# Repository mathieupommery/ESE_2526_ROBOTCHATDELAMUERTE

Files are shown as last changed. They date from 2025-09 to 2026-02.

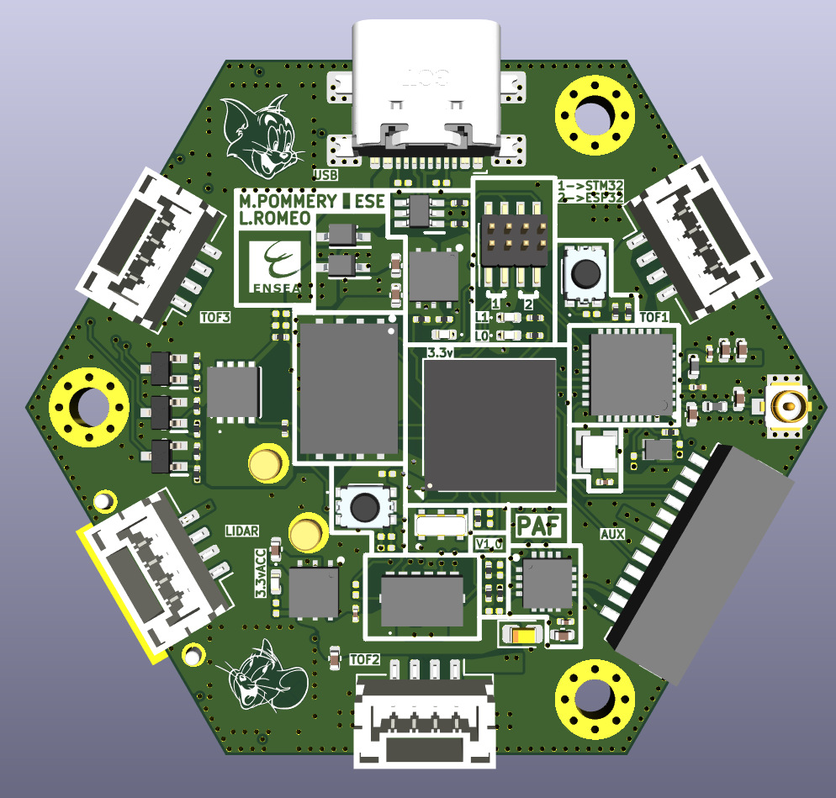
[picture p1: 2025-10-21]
DOCS/IMG README/MB_v1_front.png

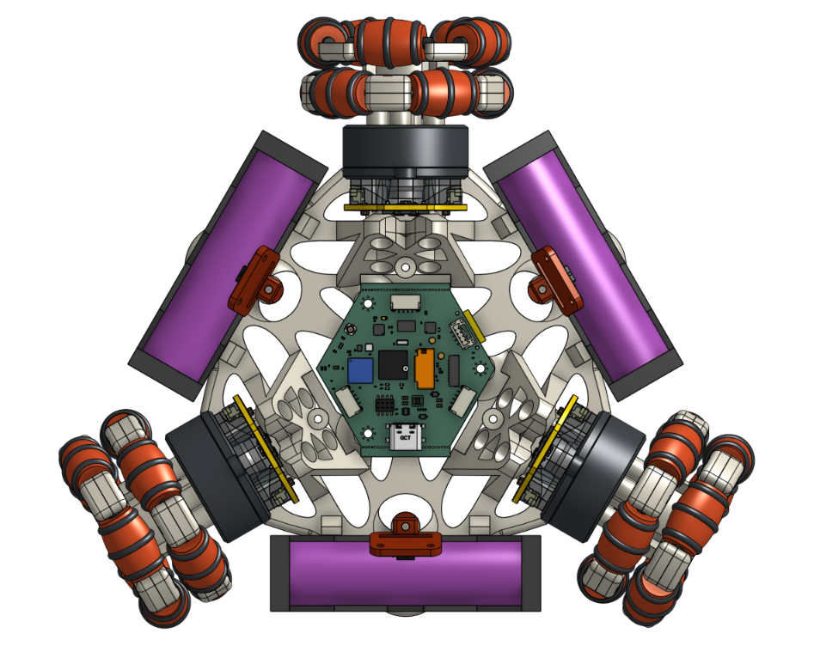
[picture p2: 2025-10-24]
DOCS/IMG README/Robot top PCB view.png

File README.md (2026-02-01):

# Cat-and-Mouse Robot Project

## Table of contents
1. [Introduction](#1-introduction)
2. [FOC omniwheel](#2-foc-omniwheel)
   1. [Hardware](#21-hardware)
      1. [Electronics](#211-electronics)
      2. [Mechanics](#212-mechanics)
   2. [Software (Overview)](#22-software-overview)
   3. [Bottleneck](#23-bottleneck)
3. [DC omniwheel](#3-dc-omniwheel)
   1. [New Motor control PCB](#31-new-motor-control-pcb)
   2. [Adapting the frame to allocate new DC motors, and more...](#32-adapting-the-frame-to-allocate-new-dc-motors-and-more)
   3. [Movement strategy](#33-movement-strategy)
      1. [Cat mode](#331-cat-mode)
      2. [Mouse mode](#332-mouse-mode)
   4. [Issues](#34-issues)
4. [Regular DC](#4-regular-dc)
   1. [Hardware](#41-hardware)
5. [Strategy Implementation](#5-strategy-implementation)
   1. [Overview of Cat/Mouse Mode](#51-overview-of-cat/mouse-mode)
   2. [LiDAR handling](#52-lidar-handling)
   3. [Motor control](#53-motor-control)
   4. [Additional PIMP mode](#54-additional-pimp-mode)

## 1. Introduction
This project aims to design and build a **mobile robotic system** capable of playing a "cat and mouse" pursuit game.  
It combines **real-time embedded control**, **sensor fusion**, and **mechanical design** to create an autonomous robot capable of chasing or evading another robot in a dynamic environment. 
In addition to that we built ESP32-S3 based audio system with the intent of **listening with a mic** and answering using **AI based model through wifi connection and online server.**

## 2. FOC omniwheel

We first wanted to make a three omniwheeled robot with FOC control on brushless motors.

### 2.1. Hardware

The hardware design is divided into two main parts:

#### 2.1.1. Electronics
The electronic subsystem provides sensing, control, and communication between the robot's components. 

##### Motherboard

###### V1
MB_v1_front

MB_v1_back

**Main features:**
- **Microcontroller:** 480Mhz STM32H743 in TFBGA100 package, 1MB RAM 2MB Flash 
- **Sensors:** ADXL343 accelerometer and 3x TOF sensor 
- **Actuators:** UART COM for each STM32 FOC controller
- **Power Management:** 2.5A 5V buck, separate 3.3V ldo between mcu and accelerometer.  
- **Communication:** SPI / UART / Wireless link via esp32-C6
- **Features:** Up to 1Gb nand flash of 512Mb Nor flash 

This board work perfectly fine on it's own, we upgraded it just for adding option and better looking connector 

###### V2
MB_v2_Front

mb_v2_back

This version improved the audio part by adding a micro sd card wich replaced the previous NOR flash in order to get faster read and write speed and easier data management (indeed nor flash work on 4096 byte secotr that has to be erased before program, it is harder to implement in order to deal with the usb msc protocol and slower) on top of that we moved all the **audio processing into a faster esp32-S3** wich communicates with the stm32 by a uart link, it allows us to get **real AI functionnality** by using wifi link and also communicate with the **STM32 that controls all of the Robot's movements**.  
Finally this board is designed as a two board stack with the FOC controller v2.

**Main features:**
- **Microcontroller:** 480Mhz STM32H743 in TFBGA100 package, 1MB RAM 2MB Flash 
- **Sensors:** ADXL343 accelerometer and 3x TOF sensor, ICS43434 I2S mems microphone 
- **Actuators:** UART COM for each STM32 FOC controller
- **Power Management:** 
-2.5A 5V buck with up to 30v input capability, -separate 3.3V ldo between for accelerometer
-latest 3.3v SIP buck from texas instrument for both mcu
- decoupling caps near motor connector.

- **Communication:** SPI / UART / Wireless link via esp32-s3 (bluetooth 5.0, wifi 2.4G)
- **Features:** Sd card port and esp32-s3 to manage all the audio part with class d amplifier max99357 and microphone in order to get AI to answer via a wifi call to an api. 

##### FOC STM32 based Controller

###### V1

Front_foc_v1
Back_foc_v1


The FOC controller is build arround a Iflight GBM2804H-100T motor, that we will use in direct drive to drive our robot using a 3 Wheel Omniwheel base. 

**Main features:**
- **Microcontroller:**  STSPIN32G0A2 built in soc with integrated STM32G031 and gate driver and opamp
- **Sensors:** MA330 absolut spi angle sensor 1uS measure time and 3us latency 
- **Features:** Uart communication to mainboard.

**encountered problem** 
This controller work very well for foc control but sensorless, indeed we the main problem is the stm32g031 itself, it don't have hardware floating point unit built in too clark and parks transform run solwer on top of that it run at only 64Mhz wich is a little slow to implement the spi communication with the MA330 on top of all calculs every 5ms.

We even tried to use only low layer librarie with prearmed dma transfer in order to cut down the cpu use in the current loop but the main problem was the lack of fpu wich even with fixed point number was hard to deal with.

In conclusion this driver is great for sensorless foc control or here for torque reason at low speed we need sensored control and we should have stepped up to the sts32ping4 but we prefer to goes in to brushed motor in order to gain time for the other problems. 

#### 2.1.2. Mechanics
The mechanical subsystem handles motion, traction, and physical interaction. 

**Main features:**
- **frame:** Lightweight 3D-printed or CNC-machined frame  
- **Drive System:** Differential or mecanum wheels for agile motion  
- **Mounts:** Sensor and board supports designed for modular assembly  
- **Simulation / CAD:** Designed on Onshape

Trimetric view of Robot CAD
Trimetric view of PCB mainboard and robot
Top view of PCB mainboard and robot

### 2.2. Software (Overview)
While hardware is the main focus, the robot also runs control and perception algorithms:

- **Real-time tasks:** Sensor acquisition, motor control, communication  
- **Sensor fusion:** Madgwick filter for attitude estimation  
- **Behavior layer:** Cat-and-mouse logic (chase / evade modes)  
- **Debug tools:** UART logs, LED indicators, optional telemetry GUI  

### 2.3. Bottleneck

However the STM32G0 are too slow for proper sensored FOC control, even after switching to low level functions, so we had to abandon using brushless motors and switch to DC ones instead to ensure that we will be able to drive the robot. 

## 3. DC omniwheel

### 3.1. New Motor control PCB

We kept the V2 Mainboard but had to drop the idea of a V2 FOC motor control board and instead use a single STSPING4 STM32 to send the PWM to the DC motor drivers.

### 3.2. Adapting the frame to allocate new DC motors, and more... 




https://github.com/user-attachments/assets/3e3c2521-501a-48cf-ad38-90644dd84529

We changed the motor mounts to accomodate the motors under the PCB stack. We therefore had to abandon the hand holding the LiDAT aesthetic to compensate for the extra space occupied byt the PCB and Motor assembly.

Nevertheless, we managed to maintain a fun look by adding a mascott Labubu holder and led strips.

### 3.3. Movement strategy

#### 3.3.1. Cat mode

The robot would behave like a "heat seeking missile" meaning that it would target the ennemy robot, thanks to a lidar filtering and clusteriwation algorithm, and move towards it while adjusting it's orientation so that the ennemy robot stays in the directional axis of the movement bearing:  



Of course the robot being three way symmetrical it would choose it's bearing axis according to the ennemy's potition so that the closest bearing gets chosen as the "front" to minimize turning time.

Table edge detection halts the robot's movement and waits for a new target (should not happen thanks to very selective filtering)

#### 3.3.2. Mouse mode

The robot would pivot in such a way that the ennemy robot is aligned with the 180 degree LiDAR bearing and maintain a distance of at least 50cm.  

Table edge is handled by "reflecting" the robot to the  largest mid-angle between the table's edge line and the approaching ennemy's relative position, much like the "bouncing DVD logo".

### 3.4. Issues

Everything was advancing relatively smoothly the PCBs were promptly assembled and tested. Despite our attention to detail we could not have anticipated the mechanical issues that would arise from the use of low temperature bismuth based soldering paste.
The solder points were not mechanically sound leading to smd connectors breaking off and even bridging in between the USART and the Power connection underneath the connector during reheating while adjusting the solder points.  This unfortunately led to the loss of several STM32H7 chips delaying our work while we searched for the issue cqused by the auxiliary PCB, whereas our assumptions were, in order of testing:
- STM32H7 BGA pads bridging
- Mainboard connector bridging
- Motor board connector bridging

Thus leading to the loss of several pricey components.

Furthermore after some time one of the encoders from the DC motors stopped working. We had to spend some precious time to try and locate the issue, resoldering components, cswapping connectors, swapping motors, debugging code. To this day the issue has not been identified with certitude, however we suspect a manufacturing issue that led to a delamination on the single, non redundant, via transmitting the encoder logic... another issue wich could not have been anticipated.

With the short time we had left we decided that assembling a new board was not ideal, especially with the fast approaching holidays and final exams, all the more if we factor in the potential breaking points of the assembly process (mechanically and thermally fragile connectors leading to the use of sub-optimal bismuth solderpaste, potential unforeseen PCB manufacturing issues). Thus, we opted for a complete mechanical redesign to avoid further time consuming and error inducing PCB assembly, moving from a three wheeled robot to a simple two wheeled robot.

## 4. Regular DC

It is with great regeret and disappointment that we opted for the failsafe route: basic geometry, relying on the leftover functionalities of our already assembled PCBs.

### 4.1. Hardware



Here is the final aesthetic of the robot, granted, this version is much less elegant and complex, but that is it's vantage point, its simplicity has allowed us to obtain a functional result, after exploring many challenging and most educational approaches. 

## 5. Strategy Implementation

### 5.1 Overview of Cat/Mouse Mode

In cat mode the robot acts like a heat seeking missile, meaning that when the Lidar detects an object the robot orients itself so that the object sits at a 180° bearing on the Lidar reading, meaning that the object is directly in front of the robot. When a 5° orientation precision is reached the robot moves forward and only stops to reorient itself if the orientation error becomes greater than 5°.

In mouse mode we adopt a pseudo-random flee method. The robot orients itself so that the cat sits behind it and moves forward when the difference in distance becomes lower than 50cm. If the side of a table is met the robot reorients itself to face the greatest half of the angle formed between the table's border and the cat's bearing position, thus always fleeing where there is more space.

### 5.2 LiDAR handling

The LiDAR is spun at roughly 8Hz guaranteeing a 1° accuracy and fast response. After parsing the RX data is stored in a 360 uiint32 long list, each index increment analog to a 1° increment, only the points ranging from 0 to 3m are stored. Then a clusterization algorithm detects and filters the objects of diameter greater than 3cm and smaller than 8cm, which could be the opposing robot's LiDAR. Then the detected clusters are classified according to their computed size in order to isolate the most likely candidate to be the ennemy's LiDAR.

### 5.3 Motor control

Two PCBs are mounted, the top one is equipped with the STM32H7 and ESP32S3 for great computing capabilities and handling Wifi and Buetooth connectivity as well as aesthetic equipments such as LEDs, Screens and Speakers. The STM32H7 communicates the movement commands to the STM32G4 mounted on the bottom PCB at a 200Hz frequency, and the bottom PCB handles the motor control PIDs and returns the speeds for the STM32H7 to compute the odometry.

### 5.4 Additional PIMP mode

In an attempt to spice things up we experimented with the cinematics of a two omniwheeled robot, more particularly its ability to drift by taking advantage of the lateral movement allowed by the rollers. Hence by advancing and turning simultaneously it is possible to crab walkj in a circle. Hence a third state that although not as elegant as a computed evasion from the cat could be used to run fast circles around the cat when in mouse mode.

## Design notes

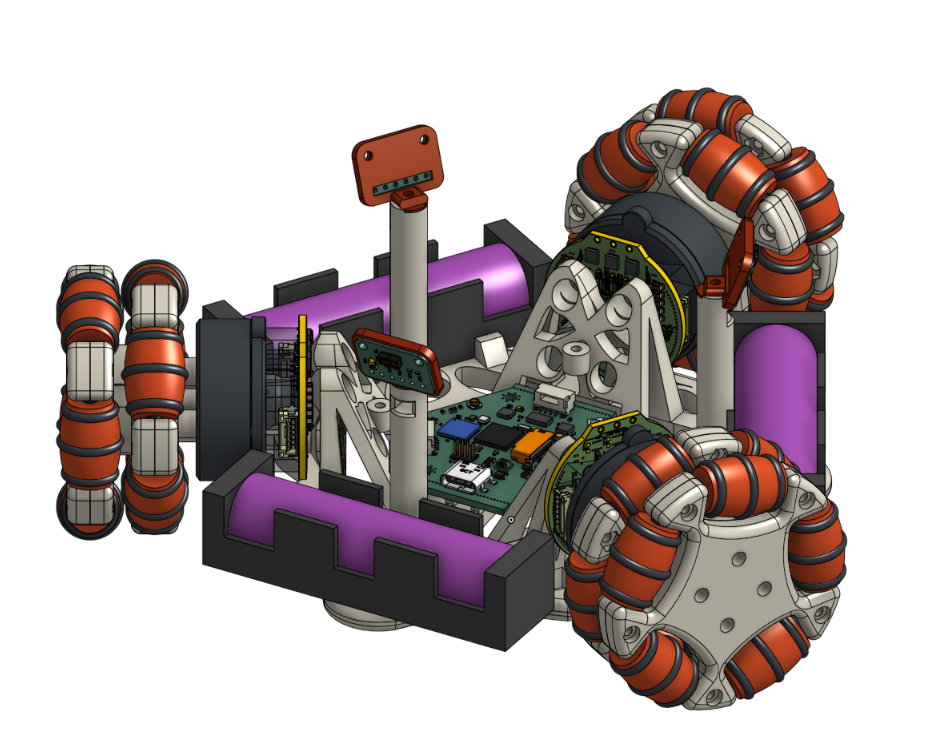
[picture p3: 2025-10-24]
DOCS/IMG README/Robot trimetrique PCB view.png

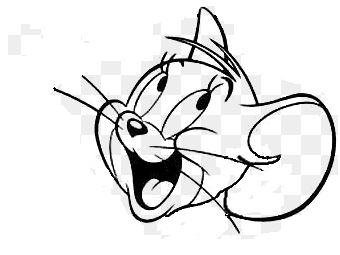
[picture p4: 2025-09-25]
DOCS/dxf/jerrytest.png

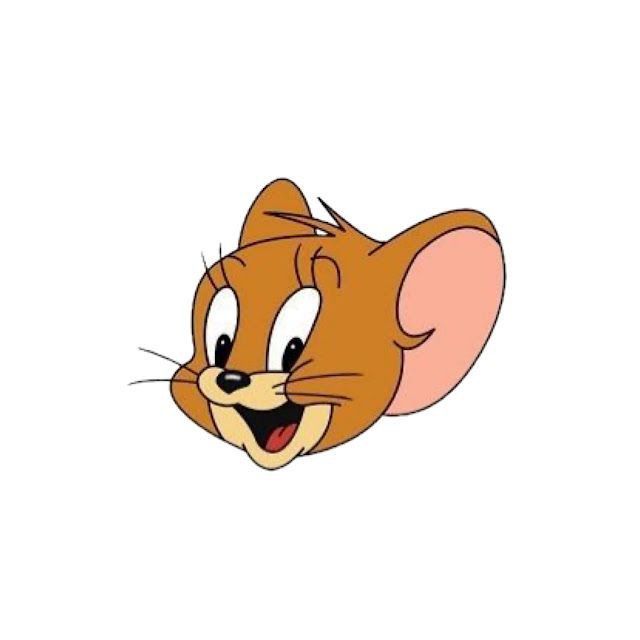
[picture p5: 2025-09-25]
DOCS/dxf/jerry.jpg

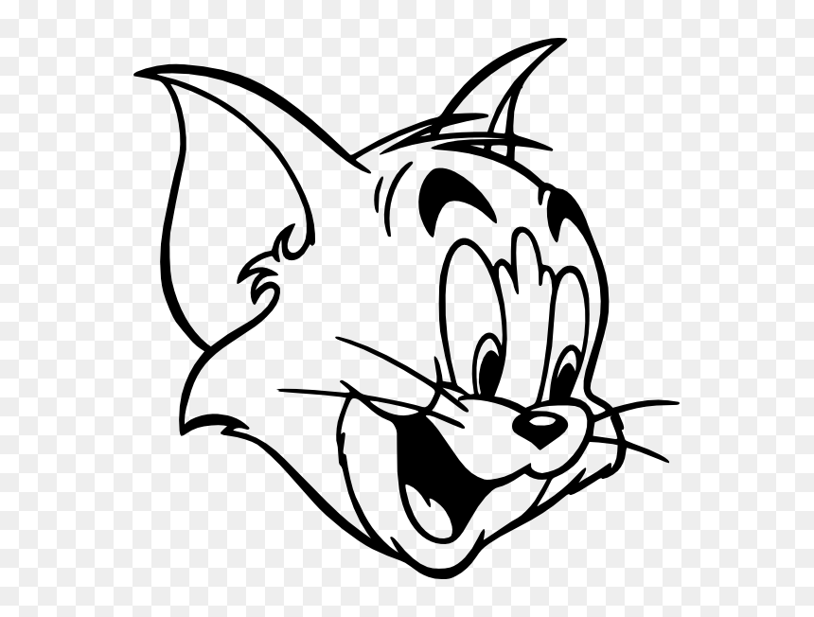
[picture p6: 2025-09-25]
DOCS/dxf/tom.png

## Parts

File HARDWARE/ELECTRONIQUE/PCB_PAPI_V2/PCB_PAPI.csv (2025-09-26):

Reference | Qty | Value | DNP | Exclude from BOM | Exclude from Board | Footprint | Datasheet
C1,C3,C5,C9,C31,C37,C42,C47 | 8 | 100n |  |  |  | samacsys:C_0201_custom | ~
C2,C14 | 2 | 4.7u |  |  |  | Capacitor_SMD:C_0402_1005Metric | ~
C4,C6,C11,C12,C17,C28,C30,C39,C41,C44 | 10 | 100n |  |  |  | Capacitor_SMD:C_0201_0603Metric | ~
C7,C10 | 2 | 2.2u |  |  |  | Capacitor_SMD:C_0402_1005Metric | ~
C8,C13,C21,C22,C23,C24,C26,C33,C36 | 9 | 1u |  |  |  | Capacitor_SMD:C_0402_1005Metric | ~
C15 | 1 | 4.7u |  |  |  | Capacitor_SMD:C_0805_2012Metric | ~
C16 | 1 | 0.1u |  |  |  | Capacitor_SMD:C_0402_1005Metric | ~
C18,C19,C20,C46,C48,C49,C50,C51,C52,C53,C54,C55 | 12 | 22u |  |  |  | Capacitor_SMD:C_0805_2012Metric | ~
C25,C45 | 2 | 10u |  |  |  | Capacitor_SMD:C_0402_1005Metric | ~
C27,C34,C35 | 3 | 10n |  |  |  | samacsys:C_0201_custom | ~
C29,C32 | 2 | TBD |  |  |  | Capacitor_SMD:C_0402_1005Metric | ~
C38,C40 | 2 | 15p |  |  |  | samacsys:C_0201_custom | ~
C43 | 1 | 10u |  |  |  | Capacitor_Tantalum_SMD:CP_EIA-1608-08_AVX-J | ~
D1 | 1 | 82400274 |  |  |  | samacsys:SOT65P210X110-6N | https://katalog.we-online.com/pbs/datasheet/82400274.pdf
D2,D3 | 2 | BAT60JFILM |  |  |  | samacsys:SOD2513X117N | https://www.mouser.jp/datasheet/2/389/cd00001944-1795661.pdf
ESC1,ESC2,ESC3 | 3 | SM08B-SRSS-TBLFSN |  |  |  | Connector_JST:JST_SHL_SM08B-SHLS-TF_1x08-1MP_P1.00mm_Horizontal
IC1 | 1 | LMR51625YFDDCR |  |  |  | samacsys:SOT95P280X110-6N | https://www.mouser.kr/ProductDetail/Texas-Instruments/LMR51625YFDDCR?qs=efUn273yAhe0Di9PgWnVVg%3D%3D
IC2,IC3 | 2 | LDO40LPU33RY |  |  |  | samacsys:SON95P300X300X90-7N-D | https://www.st.com/resource/en/datasheet/ldo40l.pdf
IC4 | 1 | ESP32-C6FH4 |  |  |  | samacsys:QFN50P500X500X90-33N | https://www.mouser.ch/ProductDetail/Espressif-Systems/ESP32-C6FH4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
IC5 | 1 | ADXL343BCCZ-RL |  |  |  | samacsys:ADXL343BCCZRL | https://www.analog.com/media/en/technical-documentation/data-sheets/ADXL343.pdf
IC6 | 1 | MAX98357AETE+ |  |  |  | samacsys:QFN50P300X300X80-17N | https://datasheets.maximintegrated.com/en/ds/MAX98357A-MAX98357B.pdf
IC7 | 1 | W25Q128JVPIQ_TR |  |  |  | samacsys:SON127P800X600X80-9N-D | https://www.winbond.com/resource-files/w25q128jv%20revf%2003272018%20plus.pdf
J1 | 1 | USB4110-GF-A |  |  |  | Connector_USB:USB_C_Receptacle_GCT_USB4110 | https://www.usb.org/sites/default/files/documents/usb_type-c.zip
J2 | 1 | 636101111001 |  |  |  | samacsys:636101111001 | https://www.we-online.com/components/products/datasheet/636101111001.pdf
J3 | 1 | XT30PW-M |  |  |  | samacsys:XT30PWM | https://www.tme.eu/sl/Document/ce4077e36b79046da520ca73227e15de/XT30PW%20SPEC.pdf
J4 | 1 | SM02B-GHS-TB_LF__SN_ |  |  |  | samacsys:SM02BGHSTBLFSN | https://datasheet.datasheetarchive.com/originals/distributors/Datasheets_SAMA/e4ef010dc292ea31091454f6c0afb63a.pdf
J5 | 1 | SM12B-SRSS-TB_LF__SN_ |  |  |  | samacsys:SM12BSRSSTBLFSN | https://www.jst-mfg.com/product/pdf/eng/eSH.pdf?67c6d96c290cd
L1 | 1 | 74438335033 |  |  |  | samacsys:INDC3030X150N | http://katalog.we-online.de/pbs/datasheet/74438335033.pdf
L2 | 1 | 2nH |  |  |  | Inductor_SMD:L_0402_1005Metric | ~
L3 | 1 | TBD |  |  |  | Inductor_SMD:L_0402_1005Metric | ~
LED1 | 1 | 587-1024-147F |  |  |  | samacsys:5871024147F | https://s3-us-west-2.amazonaws.com/catsy.557/Dialight_datasheet_587-1024-147F_Addressable_RGB.pdf
LED2,LED3 | 2 | XZMDKCBDDG45S-9 |  |  |  | samacsys:XZMDKCBDDG45S9 | http://www.sunledusa.com/products/spec/XZMDKCBDDG45S-9.pdf
LEDBLUE1 | 1 | 150040BS73240 |  |  |  | LED_SMD:LED_0402_1005Metric | ~
LEDGREEN1 | 1 | 150040GS73240 |  |  |  | LED_SMD:LED_0402_1005Metric | ~
LEDRED1,LEDRED2 | 2 | 150040RS73240 |  |  |  | LED_SMD:LED_0402_1005Metric | ~
LIDAR1,TOF1,TOF2,TOF3 | 4 | SM04B-GHE-TB |  |  |  | Connector_JST:JST_GH_BM04B-GHS-TBT_1x04-1MP_P1.25mm_Vertical
Q1 | 1 | STR2N2VH5 |  |  |  | samacsys:SOT95P255X140-3N | http://www.st.com/web/en/resource/technical/document/datasheet/DM00068028.pdf
Q2,Q4,Q5 | 3 | BSS138PW |  |  |  | samacsys:SOT65P210X110-3N | https://datasheet.datasheetarchive.com/originals/distributors/Datasheets-NXP/DSANXP010002286.pdf
Q3 | 1 | SQS401EN-T1_BE3 |  |  |  | samacsys:SQS401ENT1_BE3 | https://www.vishay.com/doc?65529
R1 | 1 | 20k |  |  |  | Resistor_SMD:R_0201_0603Metric | ~
R2,R18,R34 | 3 | 1k |  |  |  | samacsys:R_0201_custom | ~
R3,R4,R17,R23,R24,R35,R36,R37,R38 | 9 | 1k |  |  |  | Resistor_SMD:R_0201_0603Metric | ~
R5,R9,R10,R26,R27 | 5 | 22R |  |  |  | Resistor_SMD:R_0201_0603Metric | ~
R6 | 1 | 10k |  |  |  | samacsys:R_0201_custom | ~
R7,R8 | 2 | 5.1k |  |  |  | samacsys:R_0201_custom | ~
R11 | 1 | 820k |  |  |  | Resistor_SMD:R_0201_0603Metric | ~
R12 | 1 | 200k |  |  |  | samacsys:R_0201_custom | ~
R13,R33,R39,R40,R41 | 5 | 100k |  |  |  | Resistor_SMD:R_0201_0603Metric | ~
R14 | 1 | 19.1k |  |  |  | samacsys:R_0201_custom | ~
R15,R42,R43,R44 | 4 | 100R |  |  |  | Resistor_SMD:R_0201_0603Metric | ~
R16 | 1 | 100k |  |  |  | samacsys:R_0201_custom | ~
R19,R20,R28,R29 | 4 | 10k |  |  |  | Resistor_SMD:R_0201_0603Metric | ~
R21 | 1 | 20R |  |  |  | samacsys:R_0201_custom | ~
R22 | 1 | 20R |  |  |  | Resistor_SMD:R_0201_0603Metric | ~
R25 | 1 | 22R |  |  |  | samacsys:R_0201_custom | ~
R30 | 1 | 300k |  |  |  | Resistor_SMD:R_0201_0603Metric | ~
R31 | 1 | 0R |  |  |  | samacsys:R_0201_custom | ~
R32 | 1 | 0R |  |  |  | Resistor_SMD:R_0201_0603Metric | ~
S1,S2 | 2 | 435151014824 |  |  |  | samacsys:435151014824 | https://componentsearchengine.com/Datasheets/2/435151014824.pdf
SWD1 | 1 | SM04B-GHE-TB |  |  |  | Connector_JST:JST_GH_SM04B-GHS-TB_1x04-1MP_P1.25mm_Horizontal
U1 | 1 | STM32H743VIHx |  |  |  | Package_BGA:TFBGA-100_8x8mm_Layout10x10_P0.8mm | https://www.st.com/resource/en/datasheet/stm32h743vi.pdf
USBJUMP1 | 1 | Conn_01x08_Pin |  |  |  | Connector_PinHeader_1.00mm:PinHeader_2x04_P1.00mm_Vertical_SMD | ~
Y1 | 1 | CSTNE8M00GH5C000R0 |  |  |  | samacsys:CSTNE12M0GH5L000R0 | https://www.murata.com/en-us/products/productdetail.aspx?cate=cgsubResonators&partno=CSTNE8M00GH5C000R0
Y2 | 1 | LFXTAL069527REEL |  |  |  | samacsys:LFXTAL069527REEL | https://www.mouser.de/datasheet/2/741/LFXTAL069527Reel-940593.pdf

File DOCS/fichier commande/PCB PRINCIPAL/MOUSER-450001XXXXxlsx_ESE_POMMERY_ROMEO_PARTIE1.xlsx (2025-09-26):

 |  |  |  | MOUSER
Pos | I | P | Art | Désignation | Qté commandée | UA | date | Prix unitaire | Devise | Q | Grpe
10 | Z |  |  | 710-885012104005 | 500 | PC | 26.09.2025 | 0.02 | EUR | PC | TA.01 | 4161196
20 | Z |  |  | 81-GRM21BZ71E475ME5L | 10 | PC | 26.09.2025 | 0.09 | EUR | PC | TA.01
30 | Z |  | https://www.missnumerique.com/manfrotto-plateau-rapide-501pl-rectangulaire-p-1282.html | 81-GRM21BZ71A226ME5L | 40 | PC | 26.09.2025 | 0.11 | EUR | PC | TA.01
40 | Z |  |  | 710-82400274 | 3 | PC | 26.09.2025 | 0.90 | EUR | PC | TA.01
50 | Z |  |  | 511-BAT60JFILM | 10 | PC | 26.09.2025 | 0.12 | EUR | PC | TA.01
60 | Z |  |  | 306-SM08BSRSSTBLFSN | 10 | PC | 26.09.2025 | 0.93 | EUR | PC | TA.01
70 | Z |  |  | 595-LMR51625YFDDCR | 5 | PC | 26.09.2025 | 2.69 | EUR | PC | TA.01
80 | Z |  |  | 511-LDO40LPU33RY | 7 | PC | 26.09.2025 | 1.47 | EUR | PC | TA.01
90 | Z |  |  | 356-ESP32-C6FH4 | 3 | PC | 26.09.2025 | 1.94 | EUR | PC | TA.01
100 | Z |  |  | 700-MAX98357AETE+T | 3 | PC | 26.09.2025 | 2.74 | EUR | PC | TA.01
110 | Z |  |  | 454-W25Q128JVEIQ | 3 | PC | 26.09.2025 | 1.81 | EUR | PC | TA.01
120 | Z |  |  | 640-USB4110-GF-A | 3 | PC | 26.09.2025 | 1.07 | EUR | PC | TA.01
130 | Z |  |  | 710-636101111001 | 3 | PC | 26.09.2025 | 0.5 | EUR | PC | TA.01
140 | Z |  |  | 306-SM02BGHSTBLFSN | 4 | PC | 26.09.2025 | 0.29 | EUR | PC | TA.01
150 | Z |  |  | 306-SM12BSRSSTBLFSN | 4 | PC | 26.09.2025 | 0.87 | EUR | PC | TA.01
160 | Z |  |  | 710-74438335033 | 3 | PC | 26.09.2025 | 1.02 | EUR | PC | TA.01
170 | Z |  |  | 81-LQG15HH2N0C02D | 5 | PC | 26.09.2025 | 0.11 | EUR | PC | TA.01
180 | Z |  |  | 645-587-1024-147F | 3 | PC | 26.09.2025 | 0.705 | EUR | PC | TA.01
190 | Z |  |  | 710-150040RS73240 | 10 |  | 26.09.2025 | 0.23
30 | Z |  | https://www.missnumerique.com/manfrotto-plateau-rapide-501pl-rectangulaire-p-1282.html | frais de port | 1 | PC | 26.09.2025 |  | EUR | PC | TA.01
 |  |  |  |  |  |  |  | 76.60
 |  |  |  |  |  |  |  | 91.92
 |  |  |  |  |  |  | total HT
 |  |  |  |  |  |  | total TTC
MODE d'EMPLOI et CODE erreurs Version 2023
1: indiquez le fournisseur ligne 1
2:remplissez pour chaque ligne commandée les 4 champs en rouge selon les règles suivantes:
 | Art
 |  |  | 2.1 | Ne mettez rien ici tout comme dans P: remplissez les zones rouges (et pas ailleurs)
 | Désignation
 |  |  | 2.2 | Ne dépassez pas les 40 caractères: il seront automatiquement effacés lors de la recopie
 |  |  | 2.3 | Mettre le code commande impérativement en premier suivi d'une courte description
 |  |  | 2.4 | Pour RS et Farnell : mettre le code commande RS ou Farnell (7 à 9 chiffres) (et pas la référence constructeur) suivie d'une courte description
 |  |  | 2.5 | Exemple: 125-4857 capa 1uF 0508
 | Qté commandée
 |  |  | 2.6 | C'est le nombre d'unités correspondant au prix unitaire
 |  |  | 2.7 | Attention il y a des pièges
 |  |  | 2.8 | avec RS par exemple on vous demande parfois de commander par lot de 5 par exemple
 |  |  | 2.9 | si vous commandez 1 lot : le nombre d'unité est alors 5 pour 1 lot et non 1
 | date
 |  |  | 2.10 | Pour la date: mettre la de date dans une semaine (jour ouvré)
 |  |  | 2.11 | La mettre au format JJ.MM.AAAA
 |  |  | 2.13 | Bien utiliser les points comme séparateur
 | prix unitaire
 |  |  | 2.14 | Le prix est le prix HT (sans la TVA 20%) en euros d'une unité | sauf pour les commandes au comptant ou chez un fournisseur étranger (EXP-TECH par exemple): mettez le prix TTC
 |  |  | 2.15 | arrondi au centime supérieur (0.012 euros devient 0.02!)
 |  |  | 2.16 | avec pour séparateur le point
 |  |  | 2.17 | n'utilisez pas le symbole euros d'excel
3: frais de port
 |  |  | 3.1 | ajoutez une ligne pour les frais de port
 |  |  | 3.2 | dont la désignation est "frais de port"
 |  |  | 3.3 | pas de frais de port à mettre pour RS ou Farnell
 |  |  | 3.4 | Renseignez vous pour connaître les frais de port
4: conseils complémentaires
 |  |  | 4.1 | Ne modifier que les 4 champs en rouge
 |  |  | 4.2 | Ne pas modifier le document sinon cela n'a plus aucun intérêt
 |  |  | 4.3 | Mettez les références dans le même ordre que celui de la commande
 |  |  | 4.4 | Vérifier bien sur les sites les références et les prix!
 |  |  | 4.5 | N'oubliez pas les frais de port!: ajoutez une ligne pour les mentionner
5: sauvegardez le fichier au format xls

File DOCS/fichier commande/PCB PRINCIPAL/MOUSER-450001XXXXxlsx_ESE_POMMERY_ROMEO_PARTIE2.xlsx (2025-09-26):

 |  |  |  | MOUSER
Pos | I | P | Art | Désignation | Qté commandée | UA | date | Prix unitaire | Devise | Q | Grpe
10 | Z |  |  | 306-SM04BGHETBLFSN | 12 | PC | 26.09.2025 | 0.50 | EUR | PC | TA.01 | 4161196
20 | Z |  |  | 511-STR2N2VH5 | 3 | PC | 26.09.2025 | 1.08 | EUR | PC | TA.01
30 | Z |  | https://www.missnumerique.com/manfrotto-plateau-rapide-501pl-rectangulaire-p-1282.html | 771-BSS138PW115 | 10 | PC | 26.09.2025 | 0.08 | EUR | PC | TA.01
40 | Z |  |  | 78-SQS401EN-T1_BE3 | 3 | PC | 26.09.2025 | 0.77 | EUR | PC | TA.01
50 | Z |  |  | 306-SM04BGHETBLFSN | 3 | PC | 26.09.2025 | 0.50 | EUR | PC | TA.01
60 | Z |  |  | 511-STM32H743VIH6 | 3 | PC | 26.09.2025 | 13.27 | EUR | PC | TA.01
70 | Z |  |  | 81-CSTNE8M00GH5C000R | 3 | PC | 26.09.2025 | 0.23 | EUR | PC | TA.01
80 | Z |  |  | 449-LFXTAL069527REEL | 3 | PC | 26.09.2025 | 0.81 | EUR | PC | TA.01
90 | Z |  |  |  |  | PC |  |  | EUR | PC | TA.01
100 | Z |  |  |  |  | PC |  |  | EUR | PC | TA.01
110 | Z |  |  |  |  | PC |  |  | EUR | PC | TA.01
120 | Z |  |  |  |  | PC |  |  | EUR | PC | TA.01
130 | Z |  |  |  |  | PC |  |  | EUR | PC | TA.01
140 | Z |  |  |  |  | PC |  |  | EUR | PC | TA.01
150 | Z |  |  |  |  | PC |  |  | EUR | PC | TA.01
160 | Z |  |  |  |  | PC |  |  | EUR | PC | TA.01
170 | Z |  |  |  |  | PC |  |  | EUR | PC | TA.01
180 | Z |  |  |  |  | PC |  |  | EUR | PC | TA.01
190 | Z
30 | Z |  | https://www.missnumerique.com/manfrotto-plateau-rapide-501pl-rectangulaire-p-1282.html | frais de port | 1 | PC | 26.09.2025 |  | EUR | PC | TA.01
 |  |  |  |  |  |  |  | 56.82
 |  |  |  |  |  |  |  | 68.19
 |  |  |  |  |  |  | total HT
 |  |  |  |  |  |  | total TTC
MODE d'EMPLOI et CODE erreurs Version 2023
1: indiquez le fournisseur ligne 1
2:remplissez pour chaque ligne commandée les 4 champs en rouge selon les règles suivantes:
 | Art
 |  |  | 2.1 | Ne mettez rien ici tout comme dans P: remplissez les zones rouges (et pas ailleurs)
 | Désignation
 |  |  | 2.2 | Ne dépassez pas les 40 caractères: il seront automatiquement effacés lors de la recopie
 |  |  | 2.3 | Mettre le code commande impérativement en premier suivi d'une courte description
 |  |  | 2.4 | Pour RS et Farnell : mettre le code commande RS ou Farnell (7 à 9 chiffres) (et pas la référence constructeur) suivie d'une courte description
 |  |  | 2.5 | Exemple: 125-4857 capa 1uF 0508
 | Qté commandée
 |  |  | 2.6 | C'est le nombre d'unités correspondant au prix unitaire
 |  |  | 2.7 | Attention il y a des pièges
 |  |  | 2.8 | avec RS par exemple on vous demande parfois de commander par lot de 5 par exemple
 |  |  | 2.9 | si vous commandez 1 lot : le nombre d'unité est alors 5 pour 1 lot et non 1
 | date
 |  |  | 2.10 | Pour la date: mettre la de date dans une semaine (jour ouvré)
 |  |  | 2.11 | La mettre au format JJ.MM.AAAA
 |  |  | 2.13 | Bien utiliser les points comme séparateur
 | prix unitaire
 |  |  | 2.14 | Le prix est le prix HT (sans la TVA 20%) en euros d'une unité | sauf pour les commandes au comptant ou chez un fournisseur étranger (EXP-TECH par exemple): mettez le prix TTC
 |  |  | 2.15 | arrondi au centime supérieur (0.012 euros devient 0.02!)
 |  |  | 2.16 | avec pour séparateur le point
 |  |  | 2.17 | n'utilisez pas le symbole euros d'excel
3: frais de port
 |  |  | 3.1 | ajoutez une ligne pour les frais de port
 |  |  | 3.2 | dont la désignation est "frais de port"
 |  |  | 3.3 | pas de frais de port à mettre pour RS ou Farnell
 |  |  | 3.4 | Renseignez vous pour connaître les frais de port
4: conseils complémentaires
 |  |  | 4.1 | Ne modifier que les 4 champs en rouge
 |  |  | 4.2 | Ne pas modifier le document sinon cela n'a plus aucun intérêt
 |  |  | 4.3 | Mettez les références dans le même ordre que celui de la commande
 |  |  | 4.4 | Vérifier bien sur les sites les références et les prix!
 |  |  | 4.5 | N'oubliez pas les frais de port!: ajoutez une ligne pour les mentionner
5: sauvegardez le fichier au format xls

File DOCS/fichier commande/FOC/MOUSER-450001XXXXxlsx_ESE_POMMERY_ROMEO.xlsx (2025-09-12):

 |  |  |  | MOUSER
Pos | I | P | Art | Désignation | Qté commandée | UA | date | Prix unitaire | Devise | Q | Grpe
10 | Z |  |  | 81-GRM21BR61A476ME5L | 10 | PC | 12.09.2025 | 0.25 | EUR | PC | TA.01 | 4161196
20 | Z |  |  | 710-74438335220 | 5 | PC | 12.09.2025 | 1.13 | EUR | PC | TA.01
30 | Z |  | https://www.missnumerique.com/manfrotto-plateau-rapide-501pl-rectangulaire-p-1282.html | 81-GRM188R71E224KA88 | 10 | PC | 12.09.2025 | 0.03 | EUR | PC | TA.01
40 | Z |  |  | 81-GRM188R61E106MA3D | 10 | PC | 12.09.2025 | 0.09 | EUR | PC | TA.01
50 | Z |  |  | 81-GRM21BR61E226ME4L | 50 | PC | 12.09.2025 | 0.12 | EUR | PC | TA.01
60 | Z |  |  | 81-GCM188M8EH105KE8D | 30 | PC | 12.09.2025 | 0.11 | EUR | PC | TA.01
70 | Z |  |  | 511-STPS0560Z | 5 | PC | 12.09.2025 | 0.17 | EUR | PC | TA.01
80 | Z |  |  | 511-STSPIN32G0A2 | 5 | PC | 12.09.2025 | 2.91 | EUR | PC | TA.01
90 | Z |  |  | 946-MA330GQ-Z | 5 | PC | 12.09.2025 | 4.26 | EUR | PC | TA.01
100 | Z |  |  | 621-DMT6018LDR-7 | 15 | PC | 12.09.2025 | 0.5 | EUR | PC | TA.01
110 | Z |  |  | 710-435151014824 | 5 | PC | 12.09.2025 | 0.44 | EUR | PC | TA.01
120 | Z |  |  | 710-580060716002 | 15 | PC | 12.09.2025 | 0.4 | EUR | PC | TA.01
130 | Z |  |  | 594-NTCSC0201E3104FX | 10 | PC | 12.09.2025 | 0.05 | EUR | PC | TA.01
140 | Z |  |  |  |  | PC |  |  | EUR | PC | TA.01
150 | Z |  |  |  |  | PC |  |  | EUR | PC | TA.01
160 | Z |  |  |  |  | PC |  |  | EUR | PC | TA.01
170 | Z |  |  |  |  | PC |  |  | EUR | PC | TA.01
180 | Z |  |  |  |  | PC |  |  | EUR | PC | TA.01
190 | Z
30 | Z |  | https://www.missnumerique.com/manfrotto-plateau-rapide-501pl-rectangulaire-p-1282.html | frais de port | 1 | PC | 12.09.2025 |  | EUR | PC | TA.01
 |  |  |  |  |  |  |  | 71.54
 |  |  |  |  |  |  |  | 85.85
 |  |  |  |  |  |  | total HT
 |  |  |  |  |  |  | total TTC
MODE d'EMPLOI et CODE erreurs Version 2023
1: indiquez le fournisseur ligne 1
2:remplissez pour chaque ligne commandée les 4 champs en rouge selon les règles suivantes:
 | Art
 |  |  | 2.1 | Ne mettez rien ici tout comme dans P: remplissez les zones rouges (et pas ailleurs)
 | Désignation
 |  |  | 2.2 | Ne dépassez pas les 40 caractères: il seront automatiquement effacés lors de la recopie
 |  |  | 2.3 | Mettre le code commande impérativement en premier suivi d'une courte description
 |  |  | 2.4 | Pour RS et Farnell : mettre le code commande RS ou Farnell (7 à 9 chiffres) (et pas la référence constructeur) suivie d'une courte description
 |  |  | 2.5 | Exemple: 125-4857 capa 1uF 0508
 | Qté commandée
 |  |  | 2.6 | C'est le nombre d'unités correspondant au prix unitaire
 |  |  | 2.7 | Attention il y a des pièges
 |  |  | 2.8 | avec RS par exemple on vous demande parfois de commander par lot de 5 par exemple
 |  |  | 2.9 | si vous commandez 1 lot : le nombre d'unité est alors 5 pour 1 lot et non 1
 | date
 |  |  | 2.10 | Pour la date: mettre la de date dans une semaine (jour ouvré)
 |  |  | 2.11 | La mettre au format JJ.MM.AAAA
 |  |  | 2.13 | Bien utiliser les points comme séparateur
 | prix unitaire
 |  |  | 2.14 | Le prix est le prix HT (sans la TVA 20%) en euros d'une unité | sauf pour les commandes au comptant ou chez un fournisseur étranger (EXP-TECH par exemple): mettez le prix TTC
 |  |  | 2.15 | arrondi au centime supérieur (0.012 euros devient 0.02!)
 |  |  | 2.16 | avec pour séparateur le point
 |  |  | 2.17 | n'utilisez pas le symbole euros d'excel
3: frais de port
 |  |  | 3.1 | ajoutez une ligne pour les frais de port
 |  |  | 3.2 | dont la désignation est "frais de port"
 |  |  | 3.3 | pas de frais de port à mettre pour RS ou Farnell
 |  |  | 3.4 | Renseignez vous pour connaître les frais de port
4: conseils complémentaires
 |  |  | 4.1 | Ne modifier que les 4 champs en rouge
 |  |  | 4.2 | Ne pas modifier le document sinon cela n'a plus aucun intérêt
 |  |  | 4.3 | Mettez les références dans le même ordre que celui de la commande
 |  |  | 4.4 | Vérifier bien sur les sites les références et les prix!
 |  |  | 4.5 | N'oubliez pas les frais de port!: ajoutez une ligne pour les mentionner
5: sauvegardez le fichier au format xls

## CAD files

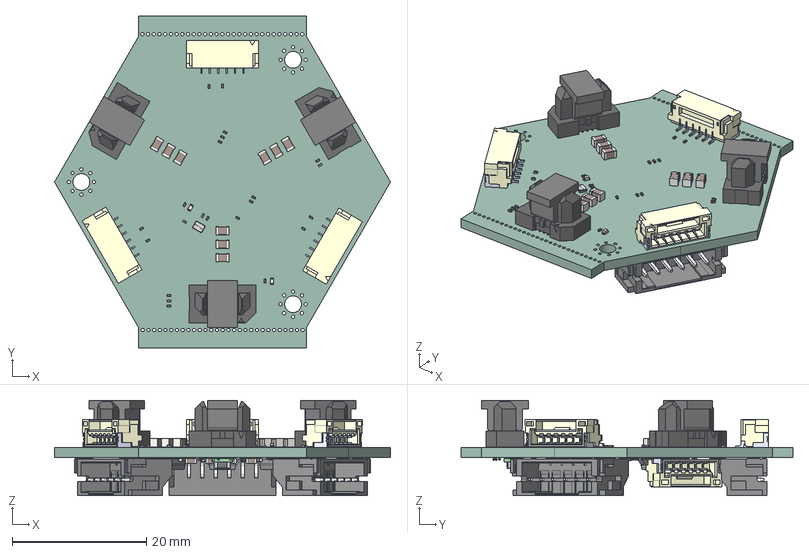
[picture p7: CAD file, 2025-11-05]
HARDWARE/ELECTRONIQUE/3D PCB/PCB_BRUSHED.step
50.0 x 49.4 x 14.2 mm
R_0201_0603Metric x 26
C_0201_0603Metric x 12
C_0805_2012Metric x 9
ERM8-005-03.0-DVT x 3
ERM8-005-03.0-DV_pin x 3
ERM8-005-03.0-DV3_pin x 3
PPP-88 x 3
SM06B-GHS-TB_LF__SN_ x 4
LED_0402_1005Metric x 2
Pins
Cover
C_0603_1608Metric x 4
C_0402_1005Metric x 6
S6B-PH-SM4-TB_LF__SN_ x 3
PinsArrayLR x 3
ThermalPad x 3
TPS82150SILR
PCB_BRUSHED_PCB

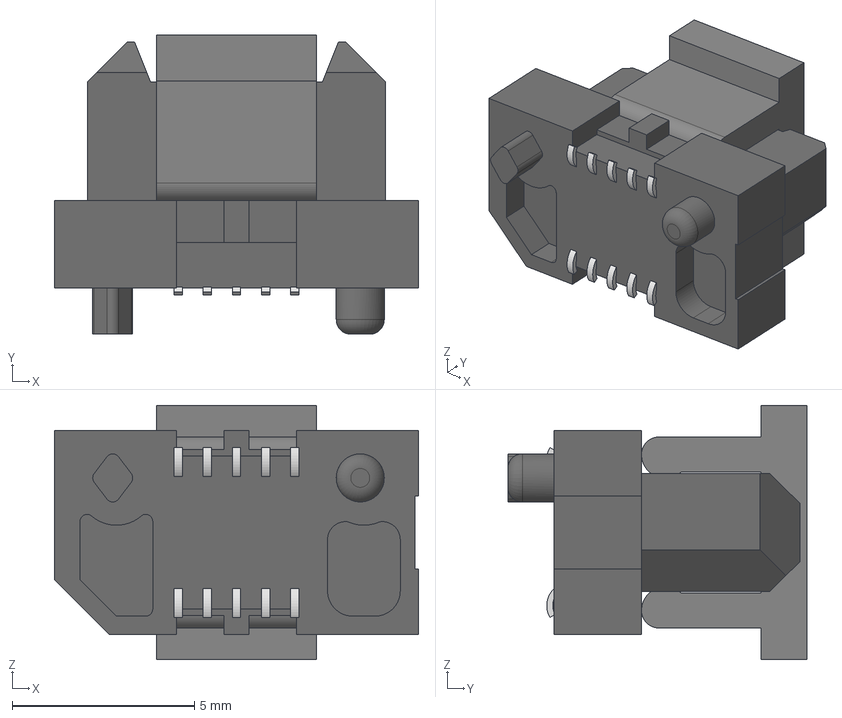
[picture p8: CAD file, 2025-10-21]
HARDWARE/ELECTRONIQUE/PCB_BRUSHED/LIB_KIKAD/ERM8/ERM8-005-03.0-L-DV-P.stp
10.0 x 8.23 x 6.99 mm
ERM8-005-03.0-DVT
ERM8-005-03.0-DV_pin
ERM8-005-03.0-DV3_pin
PPP-88

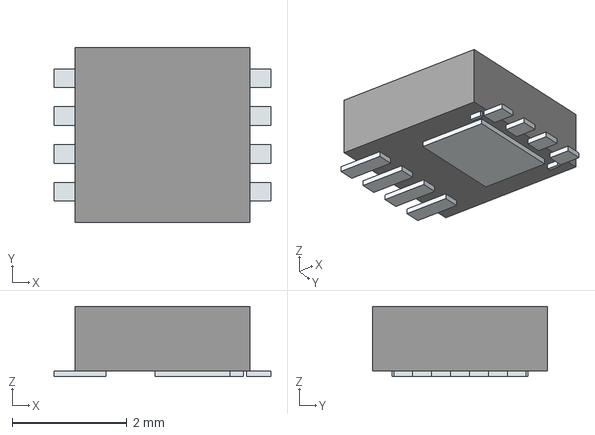
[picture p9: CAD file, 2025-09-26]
HARDWARE/ELECTRONIQUE/PCB_BRUSHED/LIB_KIKAD/libloader/SQS401EN-T1_BE3.stp
3.78 x 3.05 x 1.22 mm
Pins

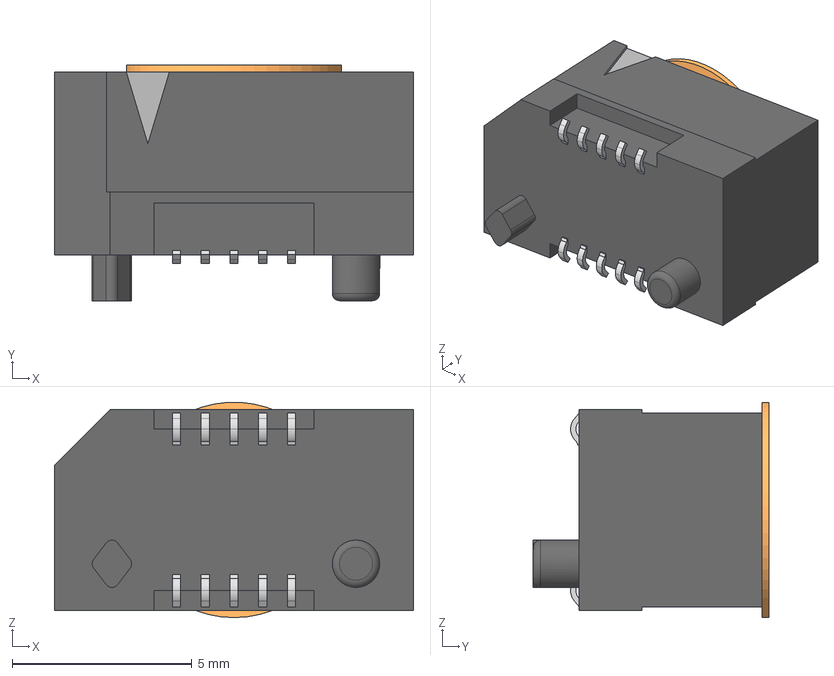
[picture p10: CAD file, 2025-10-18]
HARDWARE/ELECTRONIQUE/PCB_PAPI_V2/LIB_KIKAD/ERF8-005/ERF8-005-05.0-L-DV-K-TR.stp
10.0 x 6.56 x 5.99 mm
ERF8-005-05.0-DV-KTR
ERF8-C-211-05.0-005PN
ERF8-C-211-05.0-0052PN
ERF8-005-05.0-DVPFP

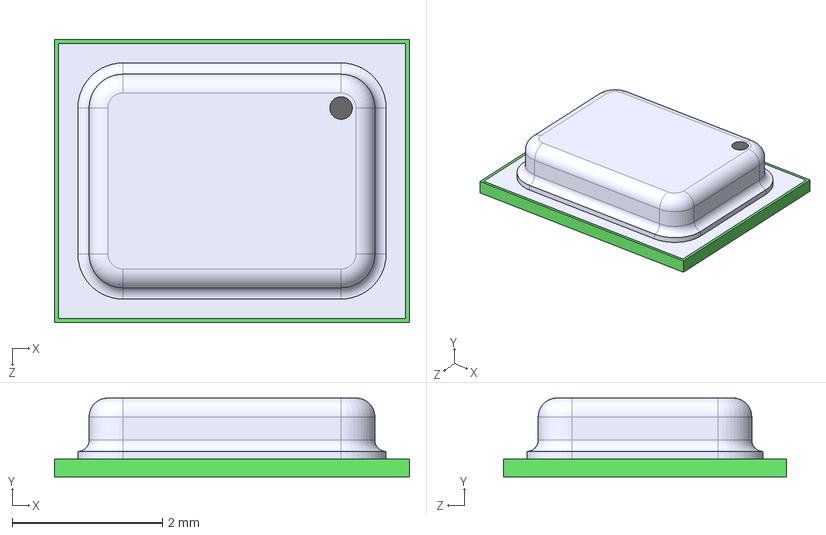
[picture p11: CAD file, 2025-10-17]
HARDWARE/ELECTRONIQUE/PCB_PAPI_V2/LIB_KIKAD/INMP441/INMP441ACEZ-R7.step
4.72 x 1.05 x 3.76 mm

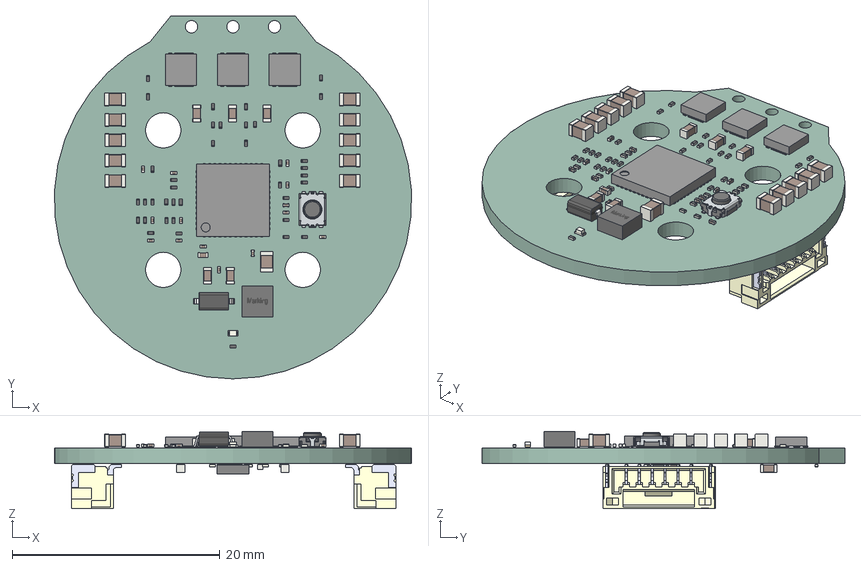
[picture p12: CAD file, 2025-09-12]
HARDWARE/FOC_CONTROLLER/FOC_CONTROLLER_V1/FOC_CONTROLLER_V1.step
34.4 x 34.9 x 7.43 mm
C_0805_2012Metric x 11
STPS0560Z
R_0201_0603Metric x 44
Base
Stem
Frame
Pin x 4
C_0201_0603Metric x 14
C_0603_1608Metric x 8
Pins x 3
body_30xx
land_pattern_30xx x 2
C_0402_1005Metric x 2
LED_0402_1005Metric
ThermalPin
PinsArrayLR
PinsArrayTB
SM06B-GHS-TB_LF__SN_ x 2
MA330GQ-Z
FOC_CONTROLLER_V1_PCB

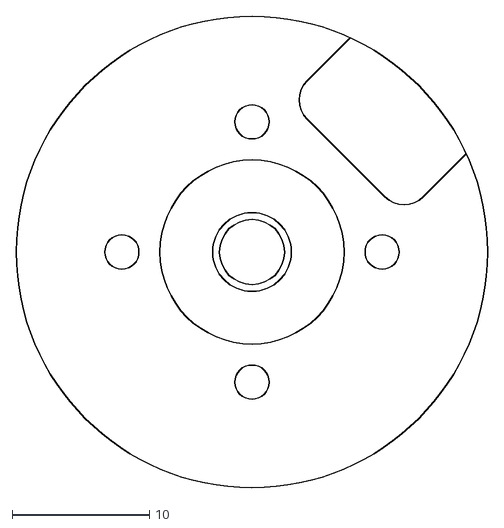
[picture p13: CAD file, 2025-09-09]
HARDWARE/MECANIQUE/MiToot 2804 100kv - stator.dxf
34.4 x 34.4

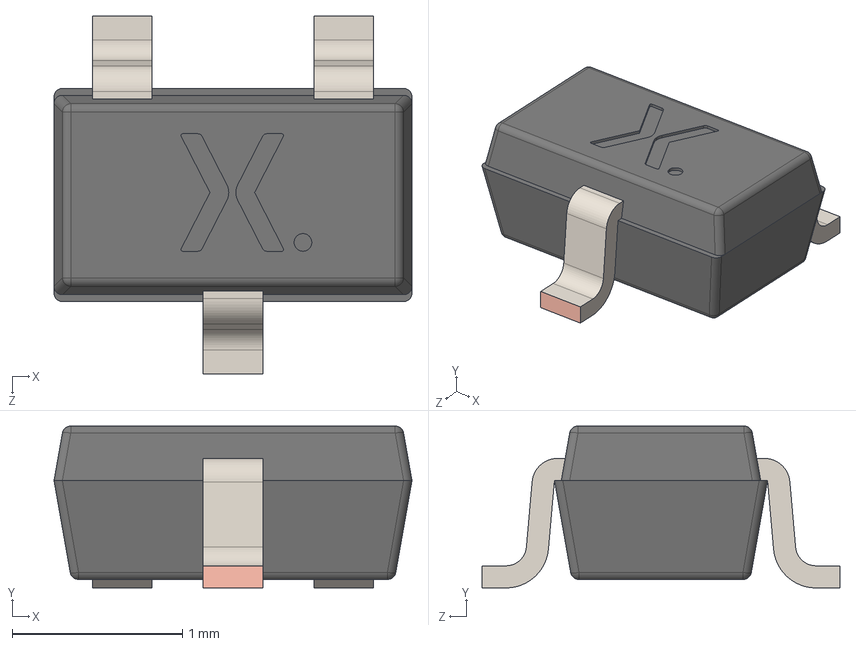
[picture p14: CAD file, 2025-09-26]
HARDWARE/ELECTRONIQUE/PCB_BRUSHED/LIB_KIKAD/libloader/BSS138PW.stp
2.10 x 0.95 x 2.10 mm
Upper body
lower body
Lead x 3

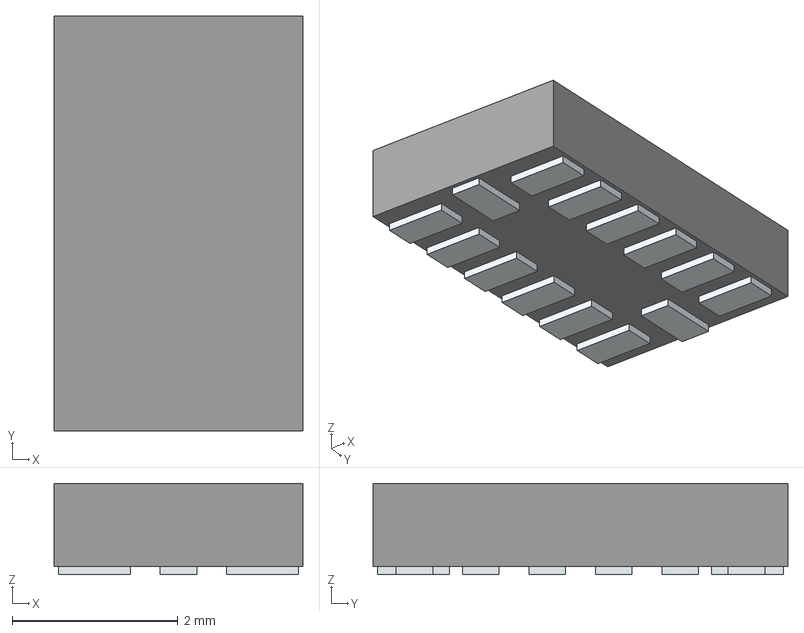
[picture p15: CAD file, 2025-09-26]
HARDWARE/ELECTRONIQUE/PCB_BRUSHED/LIB_KIKAD/libloader/ADXL343BCCZ-RL.stp
3.00 x 5.00 x 1.10 mm
Pins

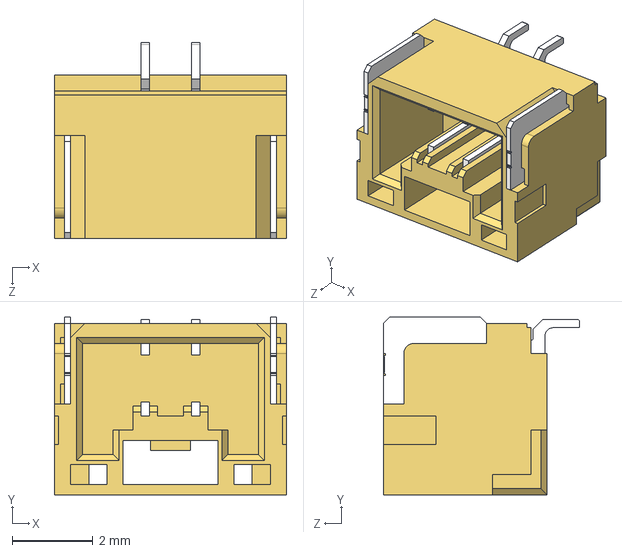
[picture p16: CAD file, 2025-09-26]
HARDWARE/ELECTRONIQUE/PCB_BRUSHED/LIB_KIKAD/libloader/SM02B-GHS-TB_LF__SN_.stp
5.75 x 4.40 x 4.85 mm

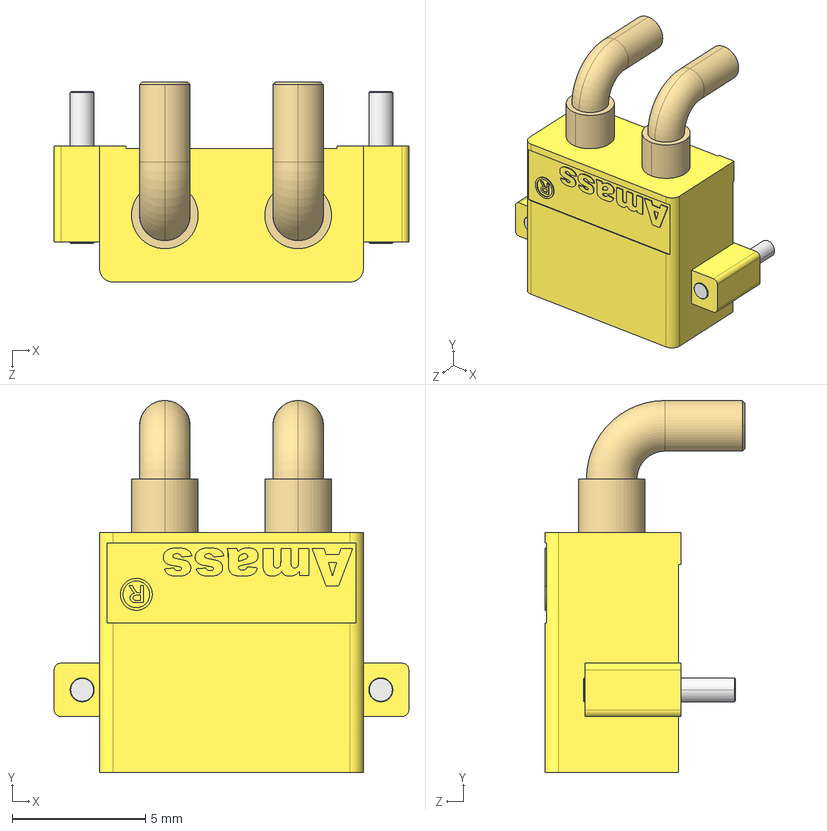
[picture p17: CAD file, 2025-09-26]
HARDWARE/ELECTRONIQUE/PCB_BRUSHED/LIB_KIKAD/libloader/XT30PW-M.stp
13.3 x 13.9 x 7.50 mm

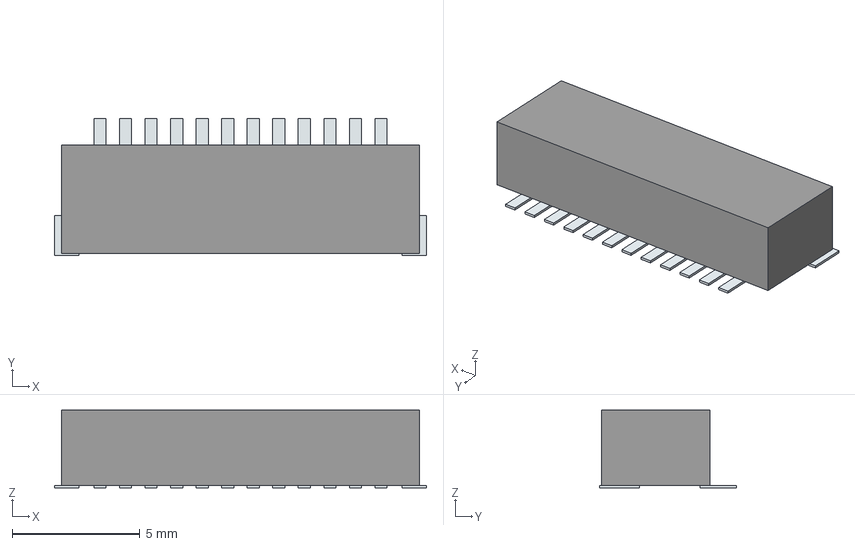
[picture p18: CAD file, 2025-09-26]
HARDWARE/ELECTRONIQUE/PCB_BRUSHED/LIB_KIKAD/libloader/SM12B-SRSS-TB_LF__SN_.stp
14.6 x 5.37 x 3.05 mm
Pins

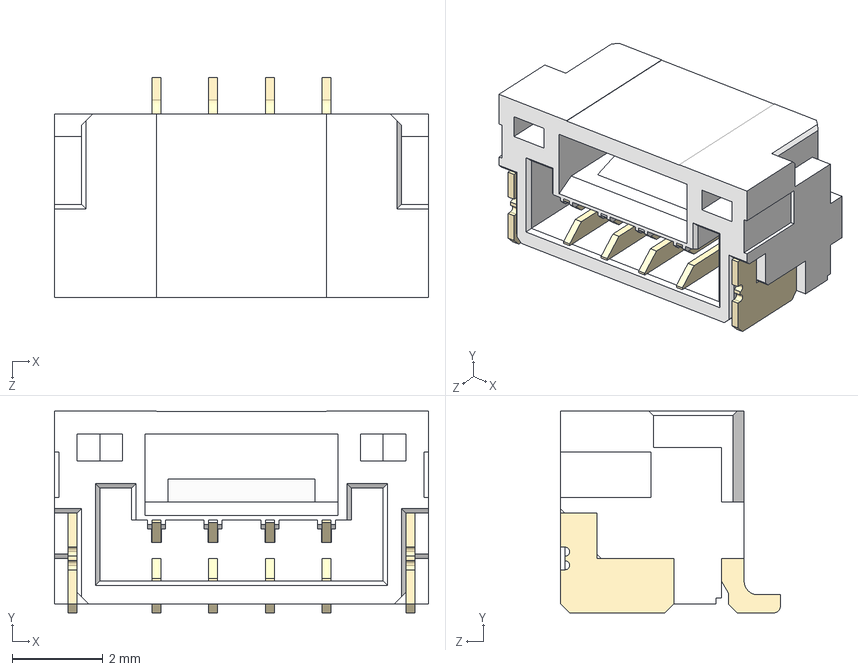
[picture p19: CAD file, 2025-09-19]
HARDWARE/ELECTRONIQUE/PCB_BRUSHED/LIB_KIKAD/libloader/SM04B-GHS-TB_LF__SN_.stp
8.25 x 4.45 x 4.85 mm

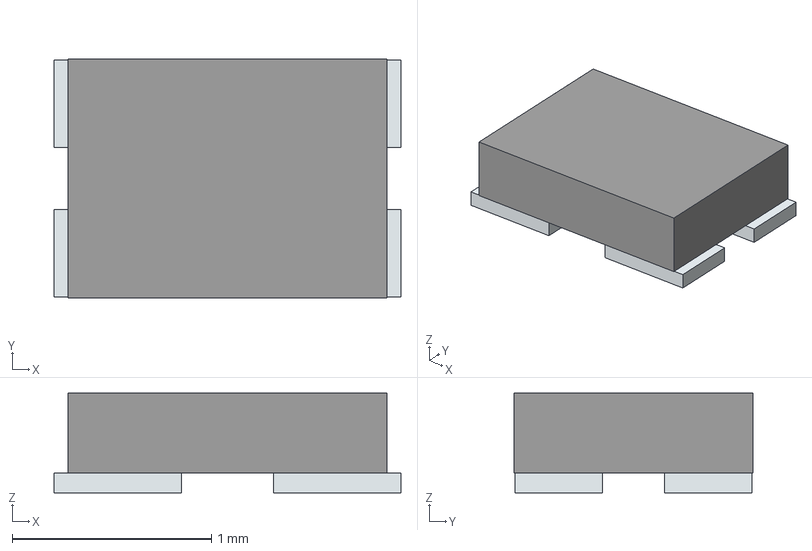
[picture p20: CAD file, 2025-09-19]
HARDWARE/ELECTRONIQUE/PCB_BRUSHED/LIB_KIKAD/libloader/LFXTAL069527REEL.stp
1.74 x 1.20 x 0.5 mm
Pins

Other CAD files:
HARDWARE/ELECTRONIQUE/3D PCB/FOC_CONTROLLER_V1.step
HARDWARE/ELECTRONIQUE/PCB_BRUSHED/LIB_KIKAD/libloader/NCV7342MW3R2G.stp
HARDWARE/ELECTRONIQUE/PCB_BRUSHED/LIB_KIKAD/libloader/W25Q16JWXHIQ_TR.stp
HARDWARE/ELECTRONIQUE/PCB_BRUSHED/LIB_KIKAD/libloader/SM08B-SRSS-TB.stp
HARDWARE/ELECTRONIQUE/PCB_BRUSHED/LIB_KIKAD/libloader/1050281001.stp
HARDWARE/ELECTRONIQUE/PCB_BRUSHED/LIB_KIKAD/libloader/2N7002KQBZ.stp
HARDWARE/ELECTRONIQUE/PCB_BRUSHED/LIB_KIKAD/libloader/3670108.stp
HARDWARE/ELECTRONIQUE/PCB_BRUSHED/LIB_KIKAD/libloader/3670148.stp
HARDWARE/ELECTRONIQUE/PCB_BRUSHED/LIB_KIKAD/libloader/435151014824.stp
HARDWARE/ELECTRONIQUE/PCB_BRUSHED/LIB_KIKAD/libloader/47309-2651.stp
HARDWARE/ELECTRONIQUE/PCB_BRUSHED/LIB_KIKAD/libloader/5871024147F.stp
HARDWARE/ELECTRONIQUE/PCB_BRUSHED/LIB_KIKAD/libloader/636101111001.stp
HARDWARE/ELECTRONIQUE/PCB_BRUSHED/LIB_KIKAD/libloader/687108183722.stp
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

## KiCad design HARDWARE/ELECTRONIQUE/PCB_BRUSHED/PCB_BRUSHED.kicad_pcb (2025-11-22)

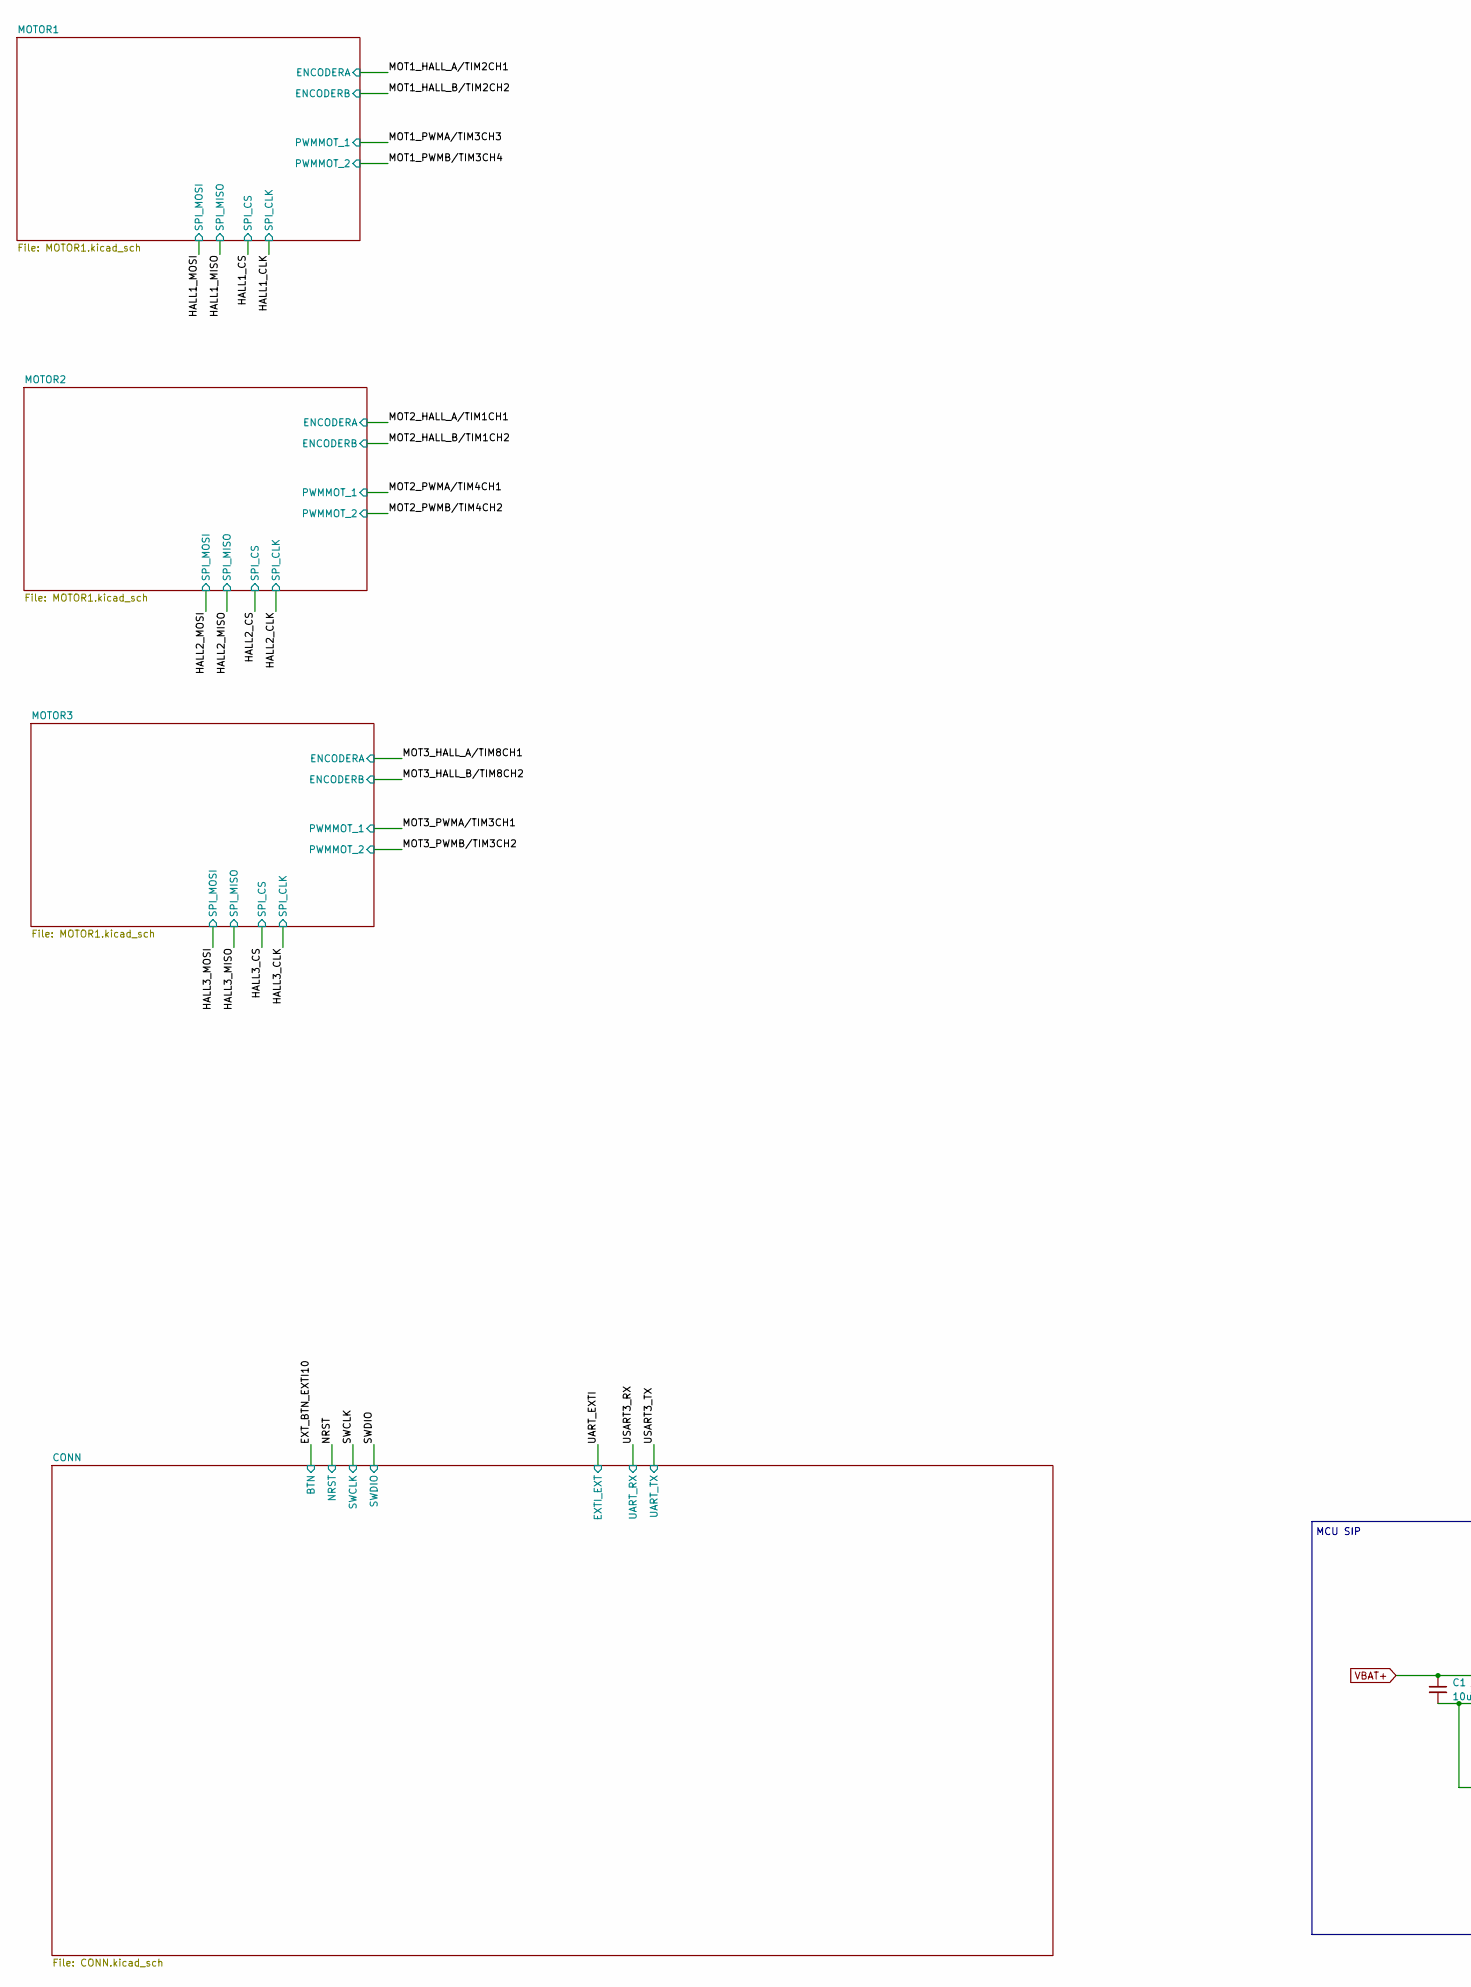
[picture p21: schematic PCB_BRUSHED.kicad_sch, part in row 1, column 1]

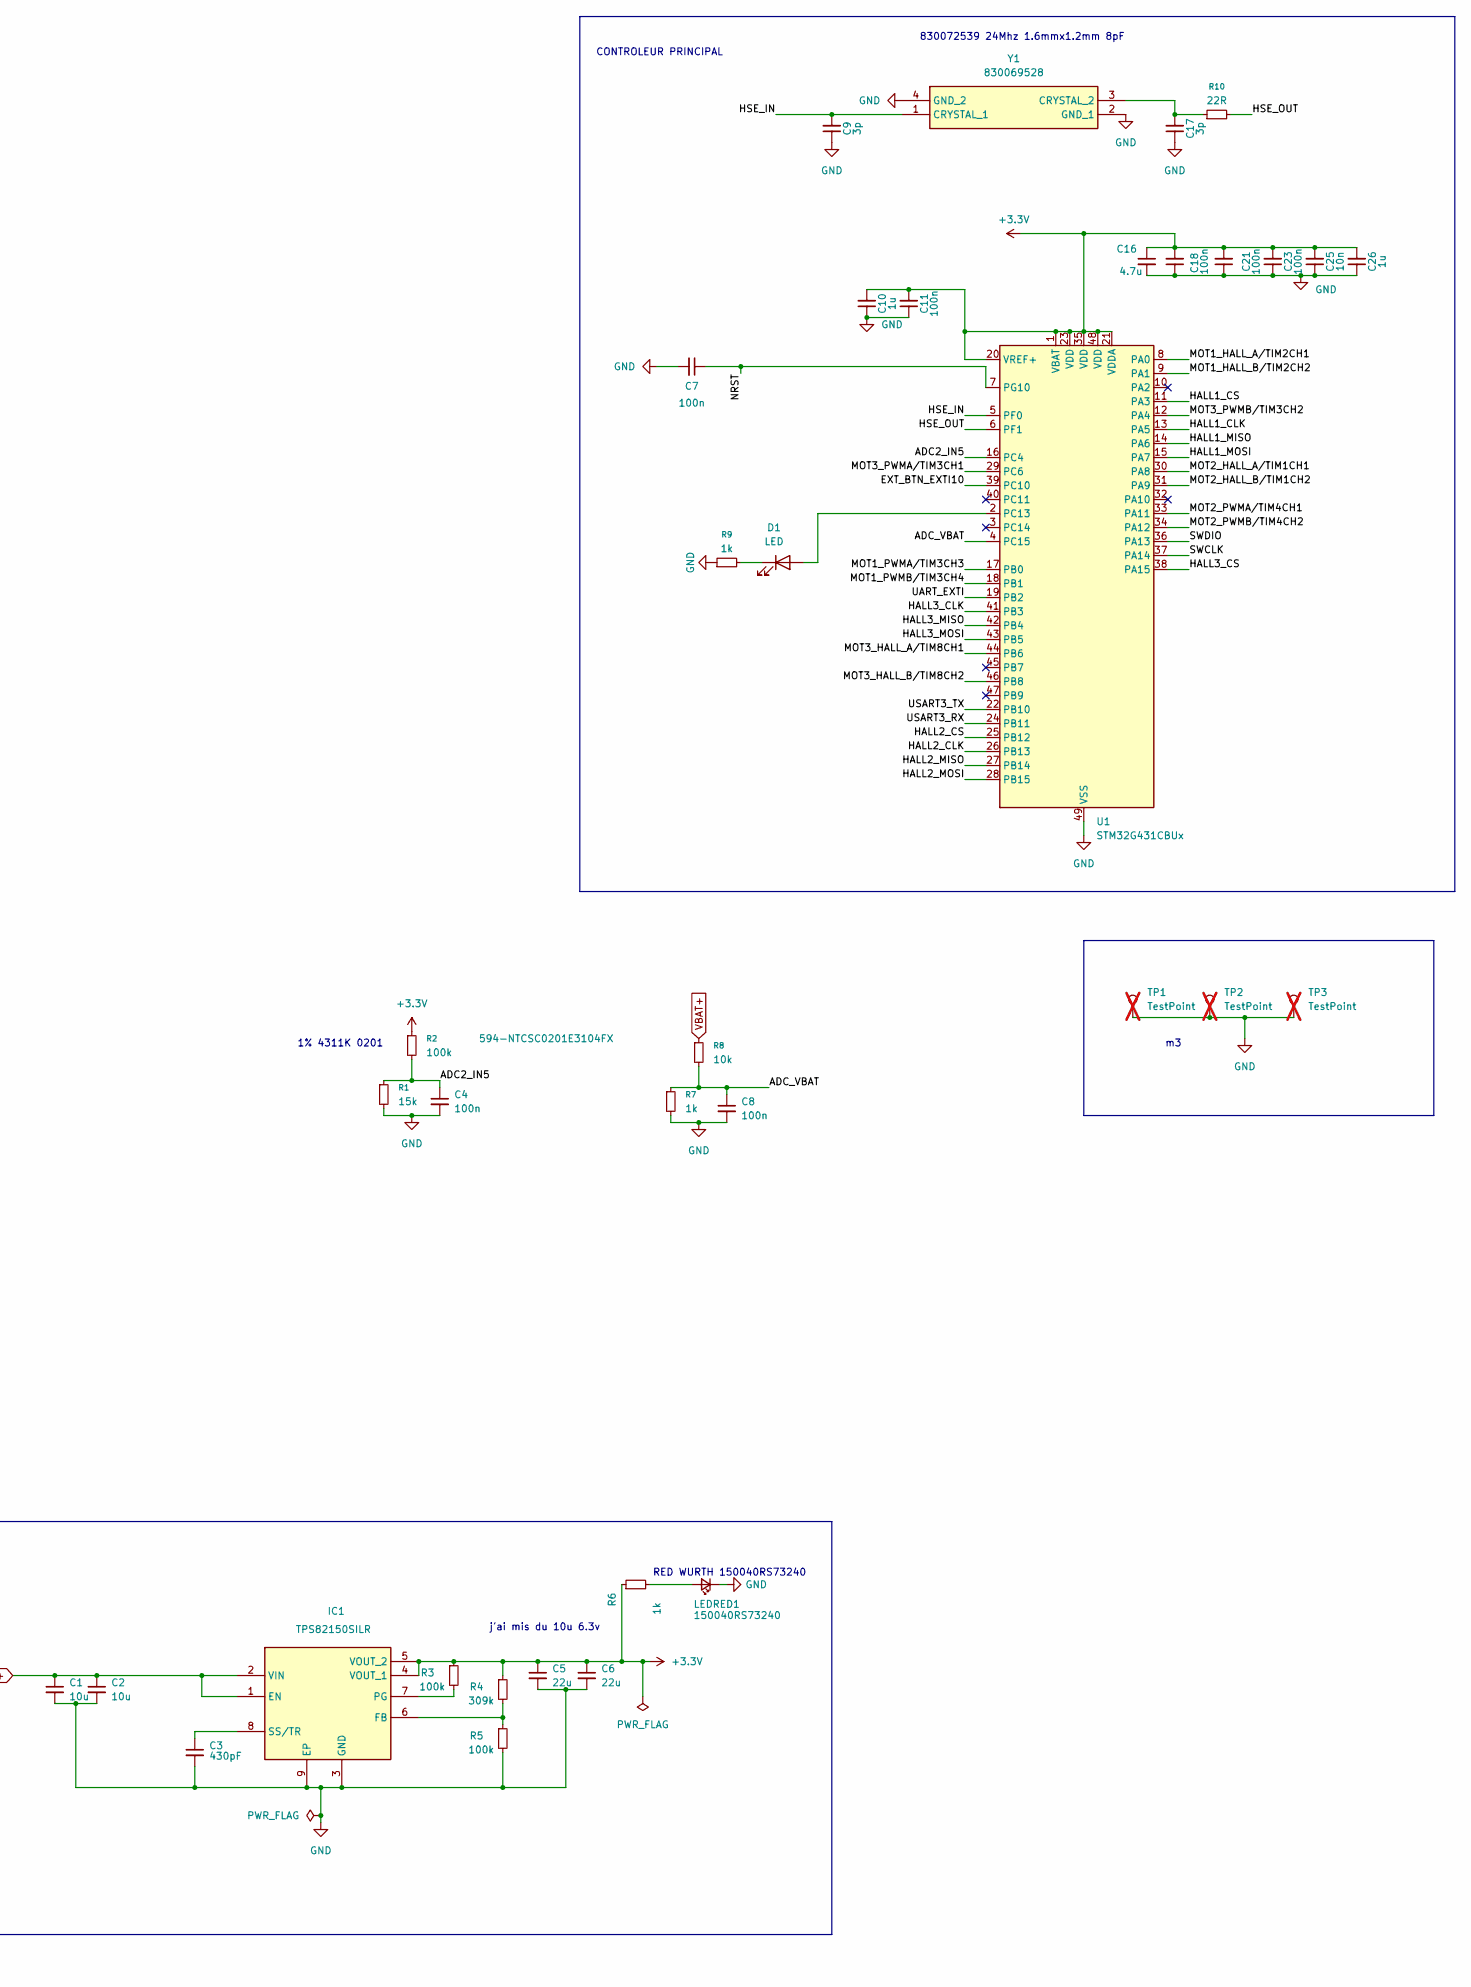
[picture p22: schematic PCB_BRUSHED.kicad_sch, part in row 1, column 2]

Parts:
C1, C2: 10u; C_0603_1608Metric; Manufacturer_Part_Number 885012105012; Mouser Part Number 710-885012105012
C3: 430pF; C_0201_0603Metric_Pad0.64x0.40mm_HandSolder
C4, C7, C8, C11, C18, C21, C23: 100n; C_0201_0603Metric_Pad0.64x0.40mm_HandSolder
C5, C6: 22u; C_0603_1608Metric; Manufacturer_Part_Number 885012105012; Mouser Part Number 710-885012105012
C9, C17: 3p; C_0201_0603Metric_Pad0.64x0.40mm_HandSolder
C10, C26: 1u; C_0402_1005Metric_Pad0.74x0.62mm_HandSolder
C16: 4.7u; C_0402_1005Metric_Pad0.74x0.62mm_HandSolder
C25: 10n; C_0201_0603Metric_Pad0.64x0.40mm_HandSolder
D1: LED; LED_0402_1005Metric
IC1: TPS82150SILR; TPS82130SILT; Manufacturer_Part_Number TPS82150SILR; Mouser Part Number 595-TPS82150SILR
LEDRED1: 150040RS73240; LED_0402_1005Metric; Manufacturer_Part_Number 150040RS73240; Mouser Part Number 710-150040RS73240
R1: 15k; R_0201_0603Metric_Pad0.64x0.40mm_HandSolder
R2: 100k; R_0201_0603Metric_Pad0.64x0.40mm_HandSolder; Manufacturer_Part_Number NTCSC0201E3104FX; Mouser Part Number 594-NTCSC0201E3104FX
R3, R5: 100k; R_0201_0603Metric_Pad0.64x0.40mm_HandSolder
R4: 309k; R_0201_0603Metric_Pad0.64x0.40mm_HandSolder
R6: 1k; R_0201_0603Metric_Pad0.64x0.40mm_HandSolder; Manufacturer_Part_Number ERJ-1GNF1001C; Mouser Part Number 667-ERJ-1GNF1001C
R7, R9: 1k; R_0201_0603Metric_Pad0.64x0.40mm_HandSolder
R8: 10k; R_0201_0603Metric_Pad0.64x0.40mm_HandSolder
R10: 22R; R_0201_0603Metric_Pad0.64x0.40mm_HandSolder
TP1, TP2, TP3: TestPoint; MountingHole_2.5mm_Pad_Via; not fitted
U1: STM32G431CBUx; QFN-48-1EP_7x7mm_P0.5mm_EP5.6x5.6mm
Y1: 830069528; Manufacturer_Part_Number 830069528; Mouser Part Number 710-830069528

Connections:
+3.3V: C5.1, C6.1, C10.2, C11.2, C16.1, C18.2, C21.2, C23.2, C25.2, C26.2, IC1.4 (VOUT_1), IC1.5 (VOUT_2), R2.1, R3.1, R4.1, R6.1, U1.1 (VBAT), U1.20 (VREF+), U1.21 (VDDA), U1.23 (VDD), U1.35 (VDD), U1.48 (VDD); also elsewhere on the board
/ADC2_IN5: C4.1, R1.1, R2.2, U1.16 (PC4)
/ADC_VBAT: C8.1, R7.1, R8.2, U1.4 (PC15)
/EXT_BTN_EXTI10: U1.39 (PC10); also elsewhere on the board
/HALL1_CLK: U1.13 (PA5); also elsewhere on the board
/HALL1_CS: U1.11 (PA3); also elsewhere on the board
/HALL1_MISO: U1.14 (PA6); also elsewhere on the board
/HALL1_MOSI: U1.15 (PA7); also elsewhere on the board
/HALL2_CLK: U1.26 (PB13); also elsewhere on the board
/HALL2_CS: U1.25 (PB12); also elsewhere on the board
/HALL2_MISO: U1.27 (PB14); also elsewhere on the board
/HALL2_MOSI: U1.28 (PB15); also elsewhere on the board
/HALL3_CLK: U1.41 (PB3); also elsewhere on the board
/HALL3_CS: U1.38 (PA15); also elsewhere on the board
/HALL3_MISO: U1.42 (PB4); also elsewhere on the board
/HALL3_MOSI: U1.43 (PB5); also elsewhere on the board
/HSE_IN: C9.2, U1.5 (PF0), Y1.1 (CRYSTAL_1)
/HSE_OUT: R10.2, U1.6 (PF1)
/MOT1_HALL_A/TIM2CH1: U1.8 (PA0); also elsewhere on the board
/MOT1_HALL_B/TIM2CH2: U1.9 (PA1); also elsewhere on the board
/MOT1_PWMA/TIM3CH3: U1.17 (PB0); also elsewhere on the board
/MOT1_PWMB/TIM3CH4: U1.18 (PB1); also elsewhere on the board
/MOT2_HALL_A/TIM1CH1: U1.30 (PA8); also elsewhere on the board
/MOT2_HALL_B/TIM1CH2: U1.31 (PA9); also elsewhere on the board
/MOT2_PWMA/TIM4CH1: U1.33 (PA11); also elsewhere on the board
/MOT2_PWMB/TIM4CH2: U1.34 (PA12); also elsewhere on the board
/MOT3_HALL_A/TIM8CH1: U1.44 (PB6); also elsewhere on the board
/MOT3_HALL_B/TIM8CH2: U1.46 (PB8); also elsewhere on the board
/MOT3_PWMA/TIM3CH1: U1.29 (PC6); also elsewhere on the board
/MOT3_PWMB/TIM3CH2: U1.12 (PA4); also elsewhere on the board
/NRST: C7.1, U1.7 (PG10); also elsewhere on the board
/SWCLK: U1.37 (PA14); also elsewhere on the board
/SWDIO: U1.36 (PA13); also elsewhere on the board
/UART_EXTI: U1.19 (PB2); also elsewhere on the board
/USART3_RX: U1.24 (PB11); also elsewhere on the board
/USART3_TX: U1.22 (PB10); also elsewhere on the board
GND: C1.2, C2.2, C3.2, C4.2, C5.2, C6.2, C7.2, C8.2, C9.1, C10.1, C11.1, C16.2, C17.1, C18.1, C21.1, C23.1, C25.1, C26.1, IC1.3 (GND), IC1.9 (EP), LEDRED1.1 (K), R1.2, R5.2, R7.2, R9.1, TP1.1, TP2.1, TP3.1, U1.49 (VSS), Y1.2 (GND_1), Y1.4 (GND_2); also elsewhere on the board
unnamed: D1.2 (A), U1.2 (PC13)
unnamed: D1.1 (K), R9.2
unnamed: IC1.6 (FB), R4.2, R5.1
unnamed: IC1.7 (PG), R3.2
unnamed: C3.1, IC1.8 (SS/TR)
unnamed: LEDRED1.2 (A), R6.2
unnamed: C17.2, R10.1, Y1.3 (CRYSTAL_2)
VBAT+: C1.1, C2.1, IC1.1 (EN), IC1.2 (VIN), R8.1; also elsewhere on the board

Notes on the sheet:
RED WURTH 150040RS73240
1% 4311K 0201
830072539 24Mhz 1.6mmx1.2mm 8pF
j'ai mis du 10u 6.3v
MCU SIP
CONTROLEUR PRINCIPAL

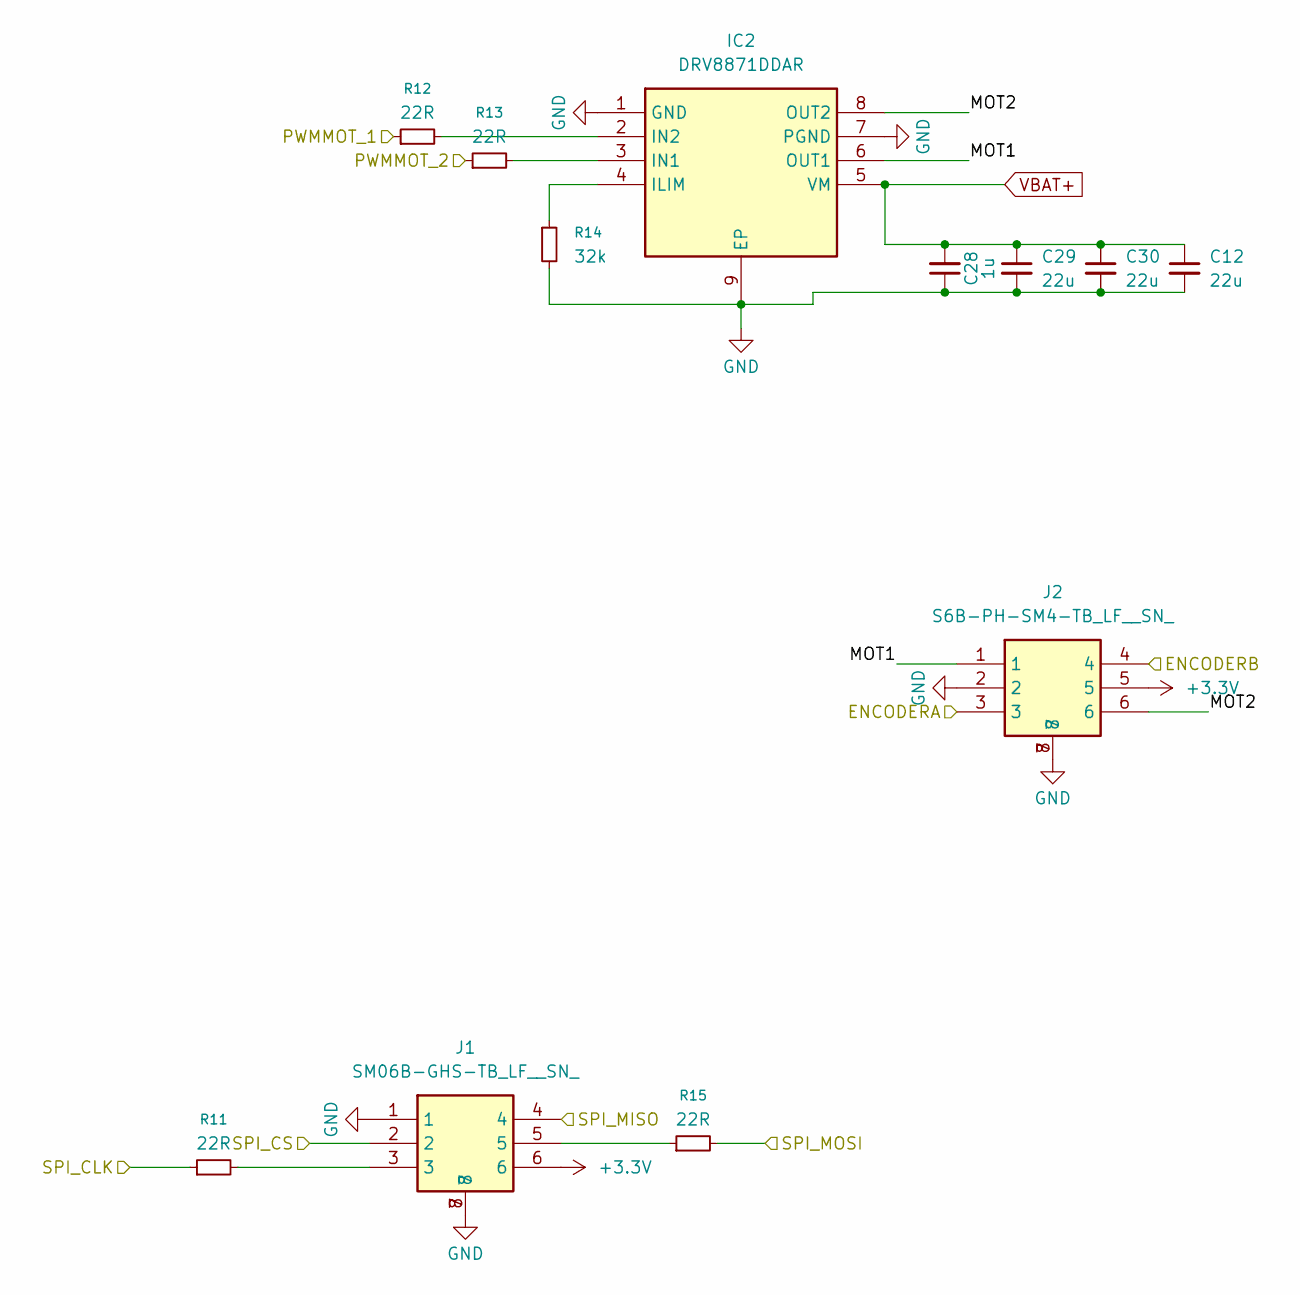
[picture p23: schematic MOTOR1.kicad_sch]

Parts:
C12, C29, C30: 22u; C_0805_2012Metric; Manufacturer_Part_Number GRM21BR61E226ME4L; Mouser Part Number 81-GRM21BR61E226ME4L
C28: 1u; C_0402_1005Metric_Pad0.74x0.62mm_HandSolder
IC2: DRV8871DDAR; SOIC127P600X170-9N; Manufacturer_Part_Number DRV8871DDAR; Mouser Part Number 595-DRV8871DDAR
J1: SM06B-GHS-TB_LF__SN_; SM06B-GHS-TB; Manufacturer_Part_Number SM06B-GHS-TB(LF)(SN); Mouser Part Number N/A
J2: S6B-PH-SM4-TB_LF__SN_; S6B-PH-SM4-TB_LF__SN__3; Manufacturer_Part_Number S6B-PH-SM4-TB(LF)(SN); Mouser Part Number N/A
R11, R12, R13, R15: 22R; R_0201_0603Metric_Pad0.64x0.40mm_HandSolder
R14: 32k; R_0201_0603Metric_Pad0.64x0.40mm_HandSolder

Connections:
+3.3V: J1.6, J2.5; also elsewhere on the board
/HALL2_CLK: R11.1; also elsewhere on the board
/HALL2_CS: J1.2; also elsewhere on the board
/HALL2_MISO: J1.4; also elsewhere on the board
/HALL2_MOSI: R15.2; also elsewhere on the board
/MOT2_HALL_A/TIM1CH1: J2.3; also elsewhere on the board
/MOT2_HALL_B/TIM1CH2: J2.4; also elsewhere on the board
/MOT2_PWMA/TIM4CH1: R12.1; also elsewhere on the board
/MOT2_PWMB/TIM4CH2: R13.1; also elsewhere on the board
/MOTOR2/MOT1: IC2.6 (OUT1), J2.1
/MOTOR2/MOT2: IC2.8 (OUT2), J2.6
GND: C12.2, C28.1, C29.2, C30.2, IC2.1 (GND), IC2.7 (PGND), IC2.9 (EP), J1.1, J1.7, J1.8, J2.2, J2.7, J2.8, R14.2; also elsewhere on the board
unnamed: IC2.4 (ILIM), R14.1
unnamed: IC2.3 (IN1), R13.2
unnamed: IC2.2 (IN2), R12.2
unnamed: J1.3, R11.2
unnamed: J1.5, R15.1
VBAT+: C12.1, C28.2, C29.1, C30.1, IC2.5 (VM); also elsewhere on the board

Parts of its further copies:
C13, C14, C32, C33, C36, C37: 22u; C_0805_2012Metric; Manufacturer_Part_Number GRM21BR61E226ME4L; Mouser Part Number 81-GRM21BR61E226ME4L
C31, C35: 1u; C_0402_1005Metric_Pad0.74x0.62mm_HandSolder
IC3, IC4: DRV8871DDAR; SOIC127P600X170-9N; Manufacturer_Part_Number DRV8871DDAR; Mouser Part Number 595-DRV8871DDAR
J3, J9: SM06B-GHS-TB_LF__SN_; SM06B-GHS-TB; Manufacturer_Part_Number SM06B-GHS-TB(LF)(SN); Mouser Part Number N/A
J4, J10: S6B-PH-SM4-TB_LF__SN_; S6B-PH-SM4-TB_LF__SN__3; Manufacturer_Part_Number S6B-PH-SM4-TB(LF)(SN); Mouser Part Number N/A
R16, R17, R18, R20, R22, R23, R24, R26: 22R; R_0201_0603Metric_Pad0.64x0.40mm_HandSolder
R19, R25: 32k; R_0201_0603Metric_Pad0.64x0.40mm_HandSolder

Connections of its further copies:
+3.3V: J3.6, J4.5, J9.6, J10.5; also elsewhere on the board
/HALL1_CLK: R16.1; also elsewhere on the board
/HALL1_CS: J3.2; also elsewhere on the board
/HALL1_MISO: J3.4; also elsewhere on the board
/HALL1_MOSI: R20.2; also elsewhere on the board
/HALL3_CLK: R22.1; also elsewhere on the board
/HALL3_CS: J9.2; also elsewhere on the board
/HALL3_MISO: J9.4; also elsewhere on the board
/HALL3_MOSI: R26.2; also elsewhere on the board
/MOT1_HALL_A/TIM2CH1: J4.3; also elsewhere on the board
/MOT1_HALL_B/TIM2CH2: J4.4; also elsewhere on the board
/MOT1_PWMA/TIM3CH3: R17.1; also elsewhere on the board
/MOT1_PWMB/TIM3CH4: R18.1; also elsewhere on the board
/MOT3_HALL_A/TIM8CH1: J10.3; also elsewhere on the board
/MOT3_HALL_B/TIM8CH2: J10.4; also elsewhere on the board
/MOT3_PWMA/TIM3CH1: R23.1; also elsewhere on the board
/MOT3_PWMB/TIM3CH2: R24.1; also elsewhere on the board
/MOTOR1/MOT1: IC3.6 (OUT1), J4.1
/MOTOR1/MOT2: IC3.8 (OUT2), J4.6
/MOTOR3/MOT1: IC4.6 (OUT1), J10.1
/MOTOR3/MOT2: IC4.8 (OUT2), J10.6
GND: C13.2, C14.2, C31.1, C32.2, C33.2, C35.1, C36.2, C37.2, IC3.1 (GND), IC3.7 (PGND), IC3.9 (EP), IC4.1 (GND), IC4.7 (PGND), IC4.9 (EP), J3.1, J3.7, J3.8, J4.2, J4.7, J4.8, J9.1, J9.7, J9.8, J10.2, J10.7, J10.8, R19.2, R25.2; also elsewhere on the board
unnamed: IC3.4 (ILIM), R19.1
unnamed: IC3.3 (IN1), R18.2
unnamed: IC3.2 (IN2), R17.2
unnamed: IC4.4 (ILIM), R25.1
unnamed: IC4.3 (IN1), R24.2
unnamed: IC4.2 (IN2), R23.2
unnamed: J3.3, R16.2
unnamed: J3.5, R20.1
unnamed: J9.3, R22.2
unnamed: J9.5, R26.1
VBAT+: C13.1, C14.1, C31.2, C32.1, C33.1, C35.2, C36.1, C37.1, IC3.5 (VM), IC4.5 (VM); also elsewhere on the board

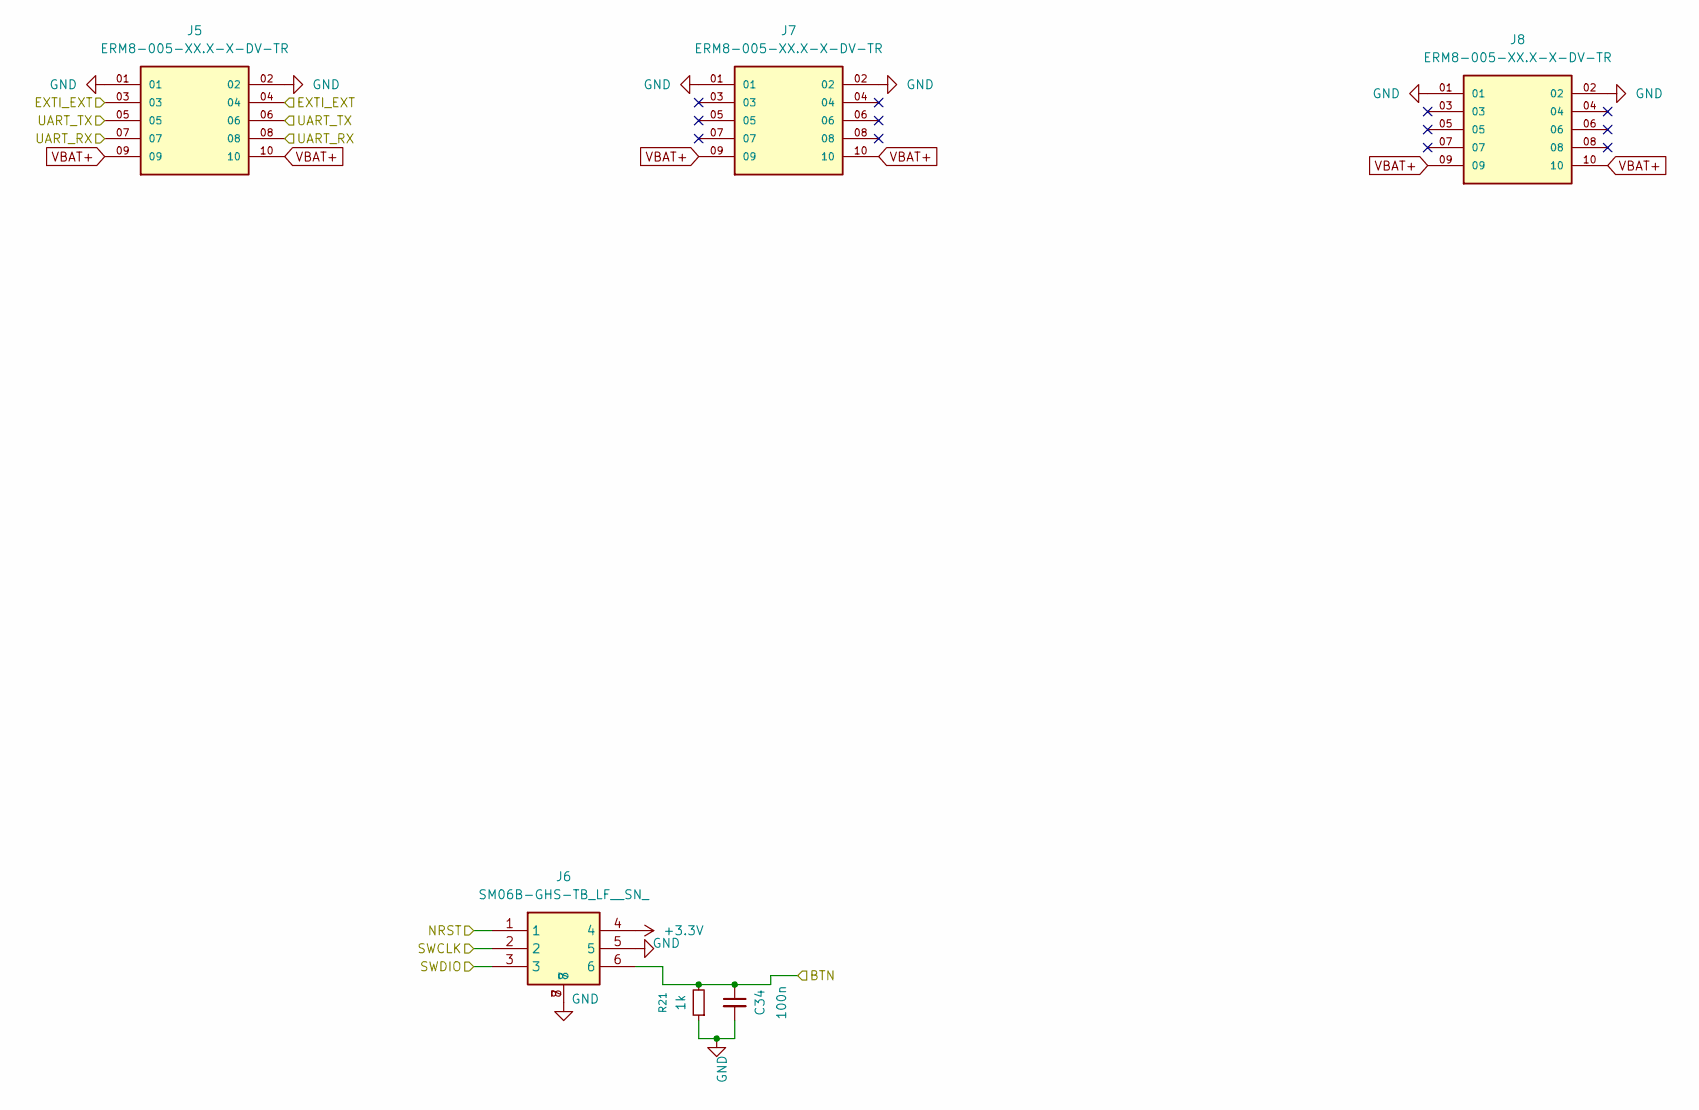
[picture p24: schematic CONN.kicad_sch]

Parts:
C34: 100n; C_0201_0603Metric_Pad0.64x0.40mm_HandSolder
J5, J7, J8: ERM8-005-XX.X-X-DV-TR; SAMTEC_ERM8-005-XX.X-X-DV-TR; PARTREV L
J6: SM06B-GHS-TB_LF__SN_; SM06B-GHS-TB; Manufacturer_Part_Number SM06B-GHS-TB(LF)(SN); Mouser Part Number N/A
R21: 1k; R_0201_0603Metric_Pad0.64x0.40mm_HandSolder

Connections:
+3.3V: J6.4; also elsewhere on the board
/EXT_BTN_EXTI10: C34.1, J6.6, R21.2; also elsewhere on the board
/NRST: J6.1; also elsewhere on the board
/SWCLK: J6.2; also elsewhere on the board
/SWDIO: J6.3; also elsewhere on the board
/UART_EXTI: J5.03, J5.04; also elsewhere on the board
/USART3_RX: J5.07, J5.08; also elsewhere on the board
/USART3_TX: J5.05, J5.06; also elsewhere on the board
GND: C34.2, J5.01, J5.02, J6.5, J6.7, J6.8, J7.01, J7.02, J8.01, J8.02, R21.1; also elsewhere on the board
VBAT+: J5.09, J5.10, J7.09, J7.10, J8.09, J8.10; also elsewhere on the board

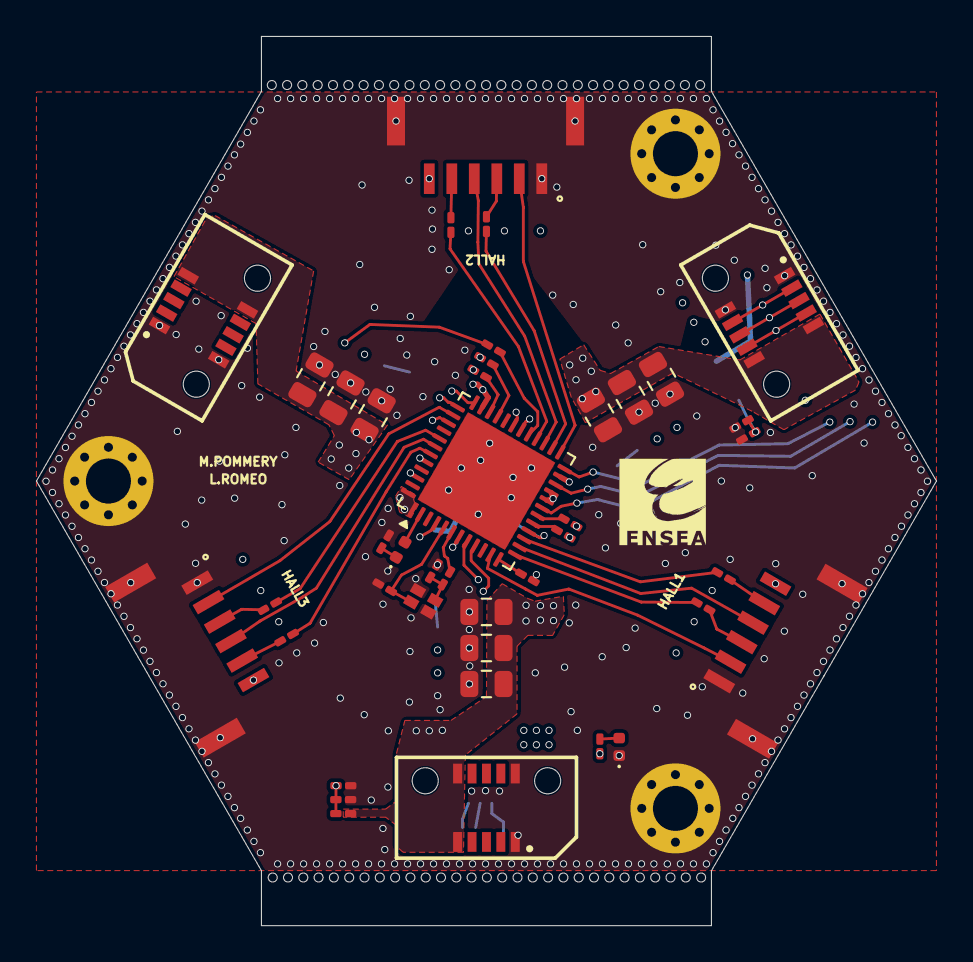
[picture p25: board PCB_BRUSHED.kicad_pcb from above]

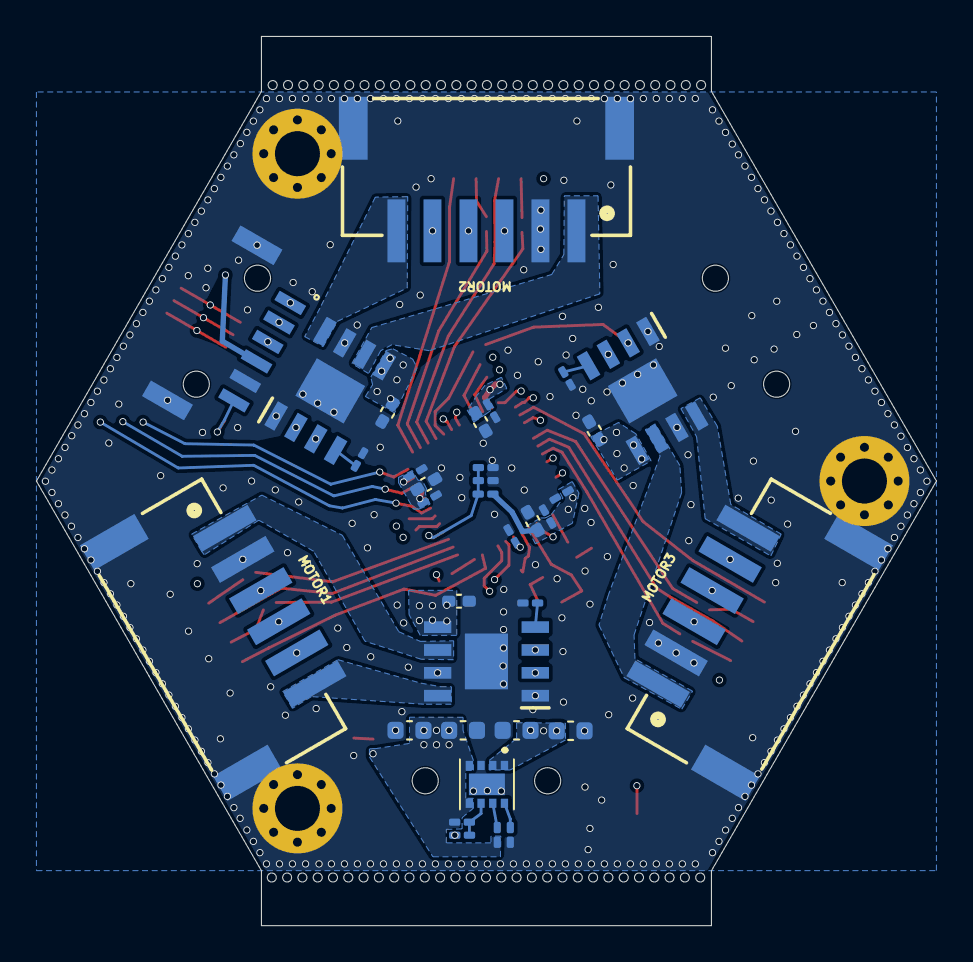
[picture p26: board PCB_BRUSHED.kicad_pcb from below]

Board: 6 copper layers, 50.0 x 49.4 mm, 78 parts (34 on the bottom side), 66 nets.

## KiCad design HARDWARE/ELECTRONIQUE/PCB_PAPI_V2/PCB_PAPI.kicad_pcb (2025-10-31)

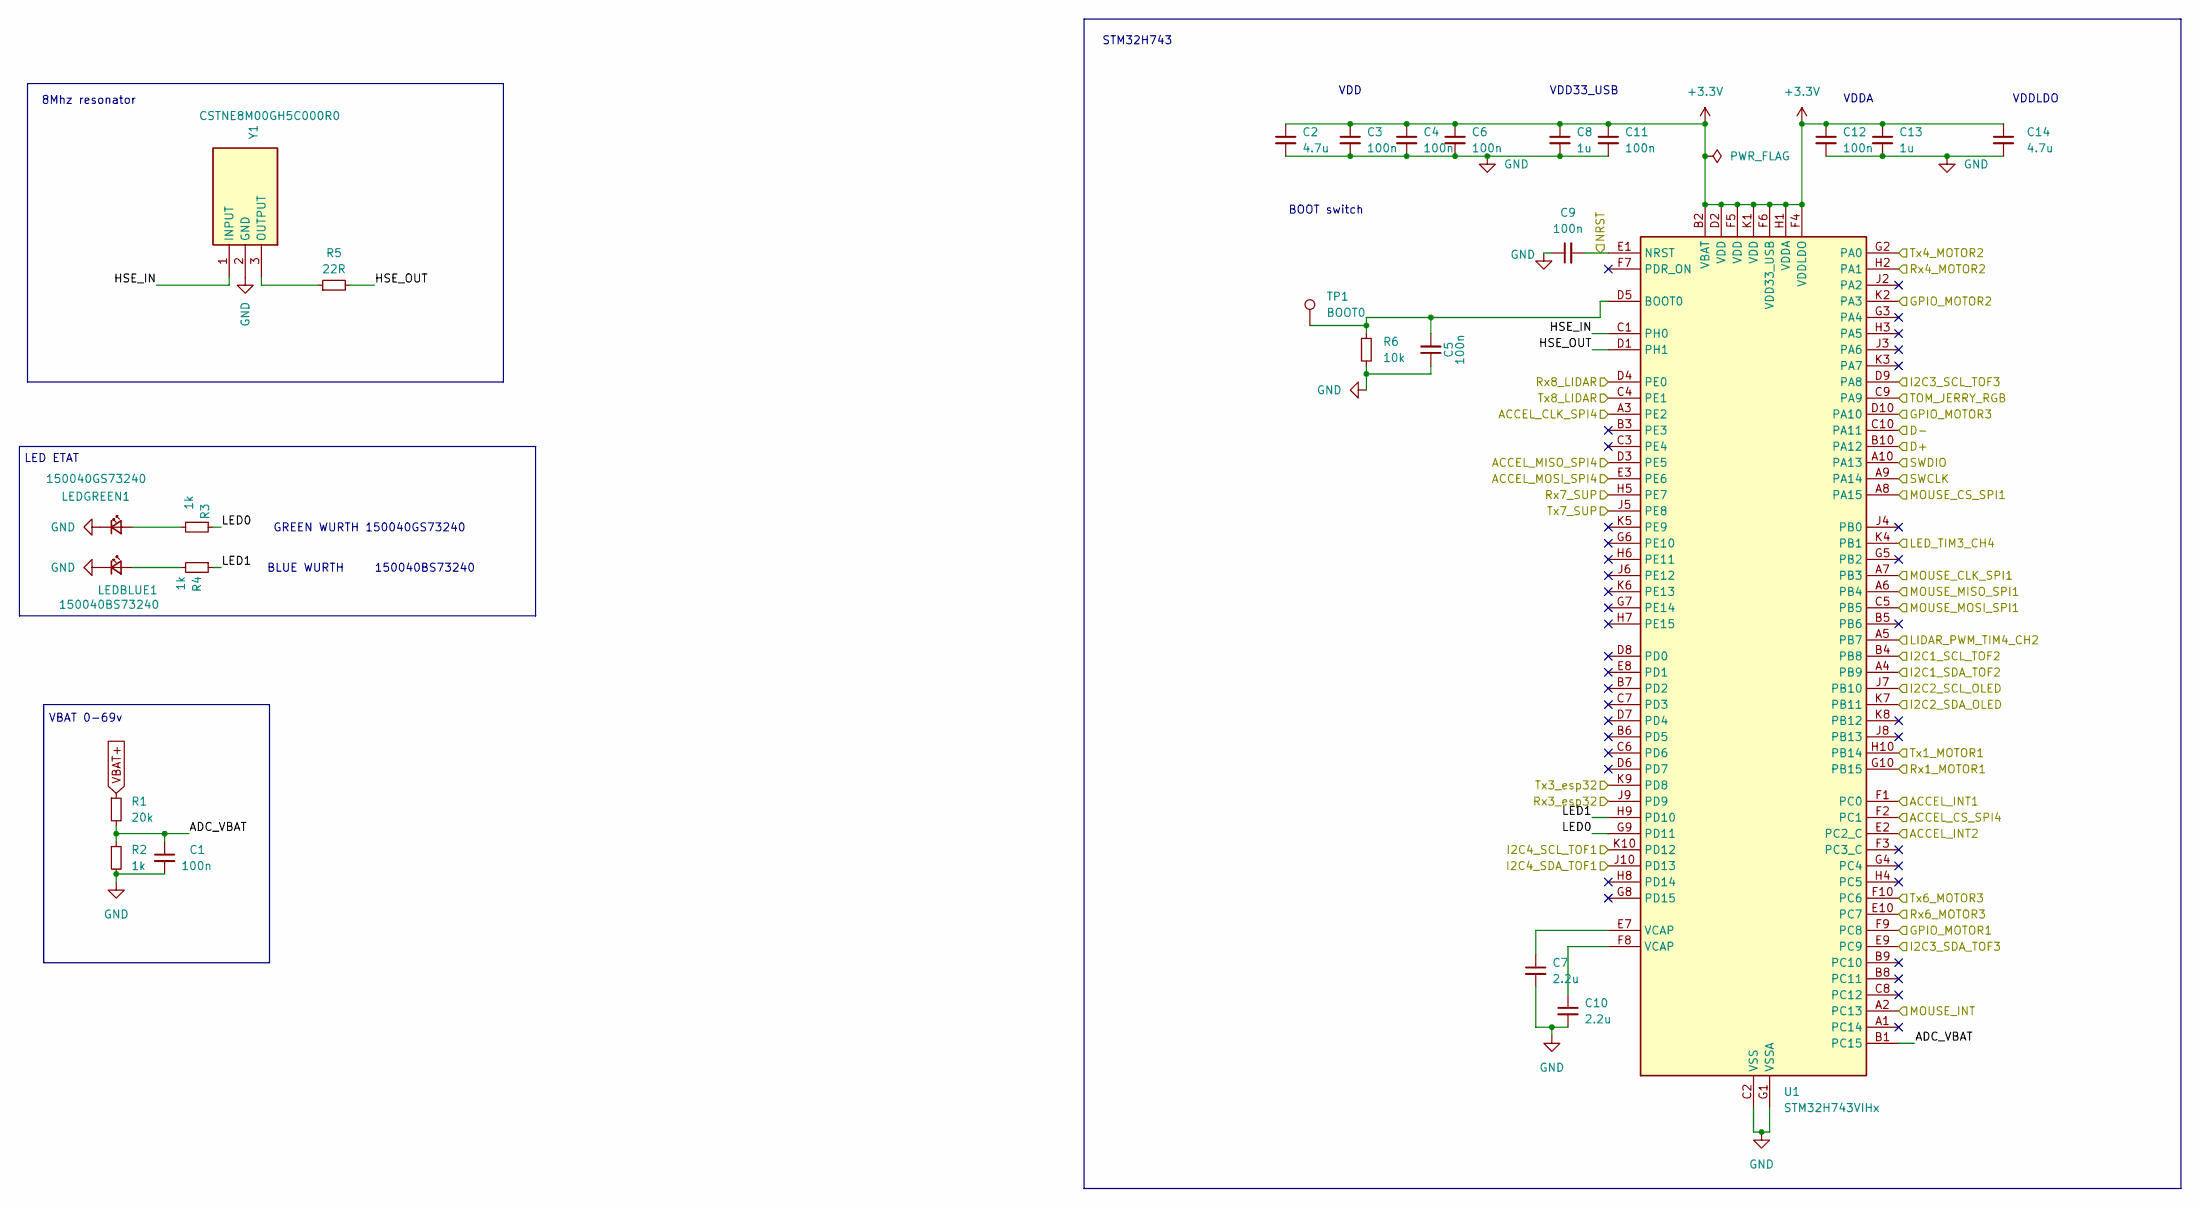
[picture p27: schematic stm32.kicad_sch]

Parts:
C1, C3, C5, C9: 100n; C_0201_custom; Manufacturer_Part_Number 885012104005; Mouser Part Number 710-885012104005
C2, C14: 4.7u; C_0402_1005Metric; Manufacturer_Part_Number 885012105008; Mouser Part Number 710-885012105008
C4, C6, C11, C12: 100n; C_0201_0603Metric; Manufacturer_Part_Number 885012104005; Mouser Part Number 710-885012104005
C7, C10: 2.2u; C_0402_1005Metric; Manufacturer_Part_Number 885012105007; Mouser Part Number 710-885012105007
C8, C13: 1u; C_0402_1005Metric; Manufacturer_Part_Number 885012105012; Mouser Part Number 710-885012105012
LEDBLUE1: 150040BS73240; LED_0402_1005Metric; Manufacturer_Part_Number 150040BS73240; Mouser Part Number 710-150040BS73240
LEDGREEN1: 150040GS73240; LED_0402_1005Metric; Manufacturer_Part_Number 150040GS73240; Mouser Part Number 710-150040GS73240
R1: 20k; R_0201_0603Metric; Manufacturer_Part_Number ERJ-1GNF2002C; Mouser Part Number 667-ERJ-1GNF2002C
R2: 1k; R_0201_custom; Manufacturer_Part_Number ERJ-1GNF1001C; Mouser Part Number 667-ERJ-1GNF1001C
R3, R4: 1k; R_0201_0603Metric; Manufacturer_Part_Number ERJ-1GNF1001C; Mouser Part Number 667-ERJ-1GNF1001C
R5: 22R; R_0201_0603Metric; Manufacturer_Part_Number ERJ-1GNF22R0C; Mouser Part Number 667-ERJ-1GNF22R0C
R6: 10k; R_0201_custom; Manufacturer_Part_Number ERJ-1GNF1002C; Mouser Part Number 667-ERJ-1GNF1002C
TP1: BOOT0; pad_0.7mm
U1: STM32H743VIHx; TFBGA-100_8x8mm_Layout10x10_P0.8mm; Manufacturer_Part_Number STM32H743VIH6; Mouser Part Number 511-STM32H743VIH6
Y1: CSTNE8M00GH5C000R0; CSTNE12M0GH5L000R0; Mouser Part Number 81-CSTNE8M00GH5C000R

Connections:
+3.3V: C2.1, C3.1, C4.1, C6.1, C8.1, C11.1, C12.1, C13.1, C14.1, U1.B2 (VBAT), U1.D2 (VDD), U1.F4 (VDDLDO), U1.F5 (VDD), U1.F6 (VDD33_USB), U1.H1 (VDDA), U1.K1 (VDD); also elsewhere on the board
/ACCEL_CLK: U1.A3 (PE2); also elsewhere on the board
/ACCEL_CS: U1.F2 (PC1); also elsewhere on the board
/ACCEL_INT1: U1.F1 (PC0); also elsewhere on the board
/ACCEL_INT2: U1.E2 (PC2_C); also elsewhere on the board
/ACCEL_MISO: U1.D3 (PE5); also elsewhere on the board
/ACCEL_MOSI: U1.E3 (PE6); also elsewhere on the board
/D+STM32: U1.B10 (PA12); also elsewhere on the board
/D-STM32: U1.C10 (PA11); also elsewhere on the board
/ESP32_RX: U1.K9 (PD8); also elsewhere on the board
/ESP32_TX: U1.J9 (PD9); also elsewhere on the board
/GPIO_MOT1: U1.F9 (PC8); also elsewhere on the board
/GPIO_MOT2: U1.K2 (PA3); also elsewhere on the board
/GPIO_MOT3: U1.D10 (PA10); also elsewhere on the board
/LED_TIM: U1.K4 (PB1); also elsewhere on the board
/LIDAR_PWM: U1.A5 (PB7); also elsewhere on the board
/MOUSE_CLK: U1.A7 (PB3); also elsewhere on the board
/MOUSE_CS: U1.A8 (PA15); also elsewhere on the board
/MOUSE_INT: U1.A2 (PC13); also elsewhere on the board
/MOUSE_MISO: U1.A6 (PB4); also elsewhere on the board
/MOUSE_MOSI: U1.C5 (PB5); also elsewhere on the board
/NRST: C9.2, U1.E1 (NRST); also elsewhere on the board
/RGB_TOM_JERRY: U1.C9 (PA9); also elsewhere on the board
/RX_LIDAR: U1.D4 (PE0); also elsewhere on the board
/RX_MOT1: U1.G10 (PB15); also elsewhere on the board
/RX_MOT2: U1.H2 (PA1); also elsewhere on the board
/RX_MOT3: U1.E10 (PC7); also elsewhere on the board
/RX_SUP: U1.H5 (PE7); also elsewhere on the board
/SCL_OLED: U1.J7 (PB10); also elsewhere on the board
/SCL_TOF1: U1.K10 (PD12); also elsewhere on the board
/SCL_TOF2: U1.B4 (PB8); also elsewhere on the board
/SCL_TOF3: U1.D9 (PA8); also elsewhere on the board
/SDA_OLED: U1.K7 (PB11); also elsewhere on the board
/SDA_TOF1: U1.J10 (PD13); also elsewhere on the board
/SDA_TOF2: U1.A4 (PB9); also elsewhere on the board
/SDA_TOF3: U1.E9 (PC9); also elsewhere on the board
/STM32/ADC_VBAT: C1.1, R1.2, R2.1, U1.B1 (PC15)
/STM32/HSE_IN: U1.C1 (PH0), Y1.1 (INPUT)
/STM32/HSE_OUT: R5.2, U1.D1 (PH1)
/STM32/LED0: R3.1, U1.G9 (PD11)
/STM32/LED1: R4.1, U1.H9 (PD10)
/STM32/Tx8_LIDAR: U1.C4 (PE1)
/SWCLK: U1.A9 (PA14); also elsewhere on the board
/SWDIO: U1.A10 (PA13); also elsewhere on the board
/TX_MOT1: U1.H10 (PB14); also elsewhere on the board
/TX_MOT2: U1.G2 (PA0); also elsewhere on the board
/TX_MOT3: U1.F10 (PC6); also elsewhere on the board
/TX_SUP: U1.J5 (PE8); also elsewhere on the board
GND: C1.2, C2.2, C3.2, C4.2, C5.1, C6.2, C7.2, C8.2, C9.1, C10.2, C11.2, C12.2, C13.2, C14.2, LEDBLUE1.1 (K), LEDGREEN1.1 (K), R2.2, R6.2, U1.C2 (VSS), U1.E4 (VSS), U1.E5 (VSS), U1.E6 (VSS), U1.G1 (VSSA), U1.J1 (VSS), Y1.2 (GND); also elsewhere on the board
unnamed: C7.1, U1.E7 (VCAP)
unnamed: C10.1, U1.F8 (VCAP)
unnamed: LEDBLUE1.2 (A), R4.2
unnamed: LEDGREEN1.2 (A), R3.2
unnamed: C5.2, R6.1, TP1.1, U1.D5 (BOOT0)
unnamed: R5.1, Y1.3 (OUTPUT)
VBAT+: R1.1; also elsewhere on the board

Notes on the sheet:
8Mhz resonator
STM32H743
VDD
GREEN WURTH 150040GS73240
VDDA
BOOT switch
LED ETAT
VDD33_USB
VBAT 0-69v
BLUE WURTH 150040BS73240
VDDLDO

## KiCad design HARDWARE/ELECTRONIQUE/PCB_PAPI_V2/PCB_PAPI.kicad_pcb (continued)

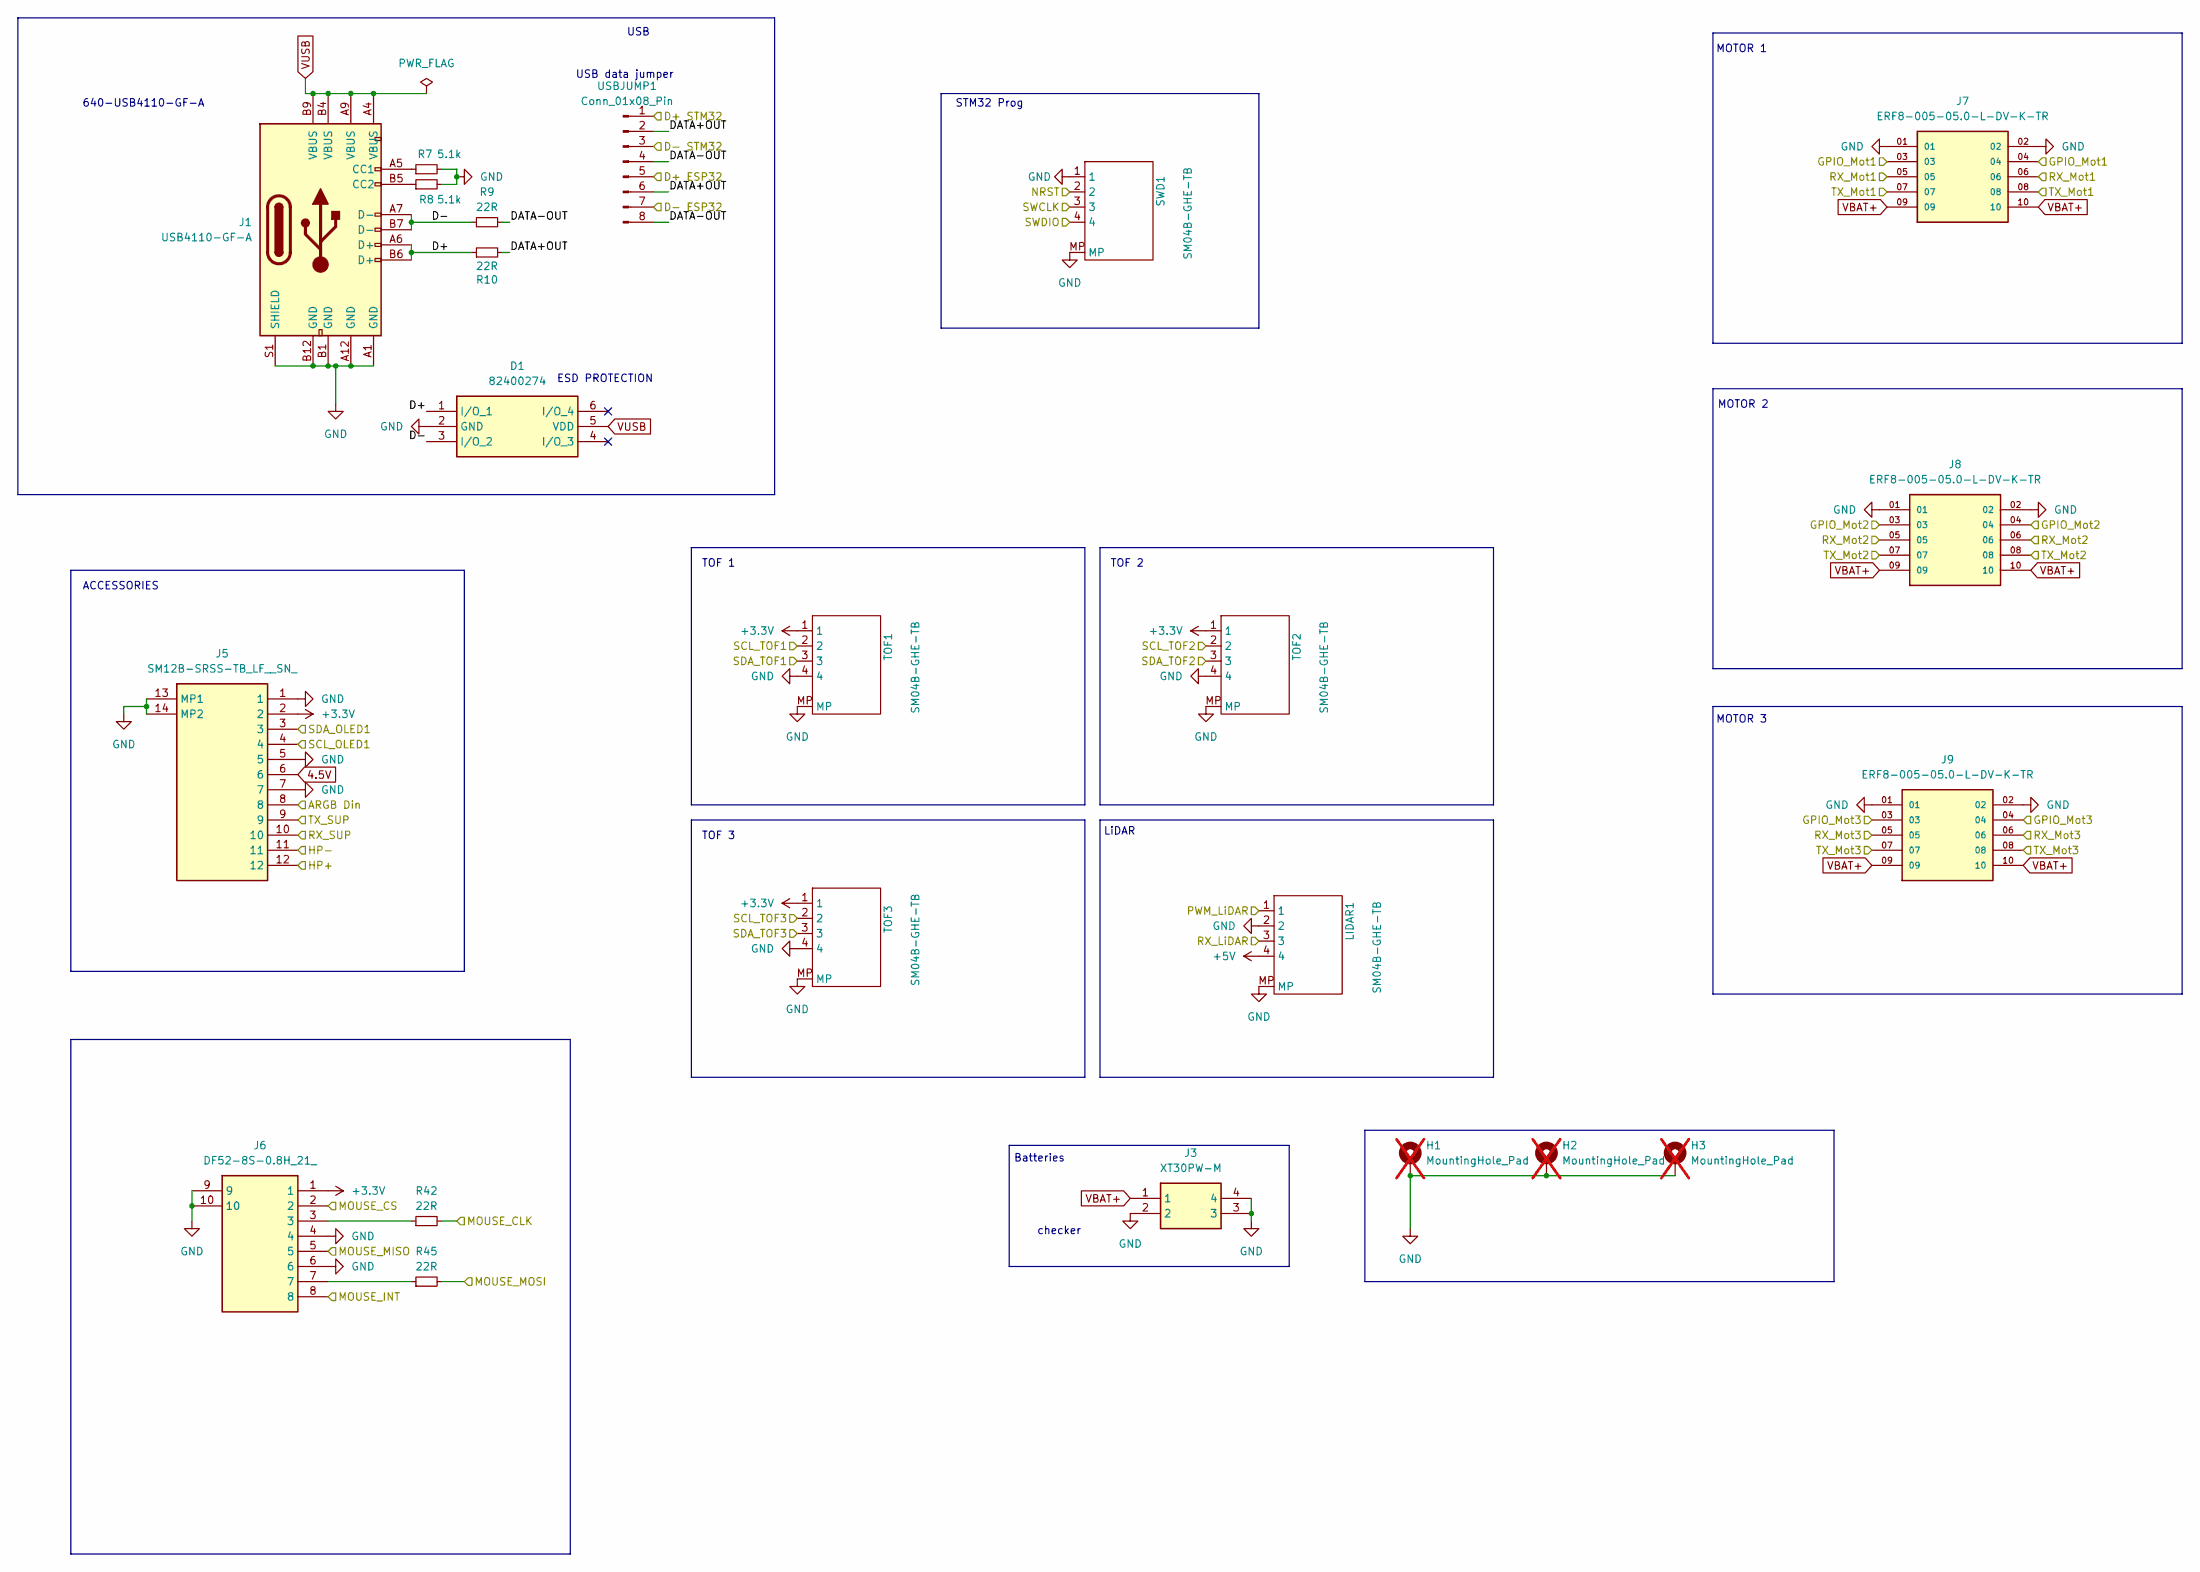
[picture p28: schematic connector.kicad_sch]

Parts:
D1: 82400274; SOT65P210X110-6N; Mouser Part Number 710-82400274
H1, H2, H3: MountingHole_Pad; MountingHole_2.5mm_Pad_Via; not fitted
J1: USB4110-GF-A; USB_C_Receptacle_GCT_USB4110; Manufacturer_Part_Number USB4110-GF-A; Mouser Part Number 640-USB4110-GF-A
J3: XT30PW-M; XT30PWM; Manufacturer_Part_Number XT30PW-M
J5: SM12B-SRSS-TB_LF__SN_; SM12BSRSSTBLFSN; Manufacturer_Part_Number SM12B-SRSS-TB(LF)(SN); Mouser Part Number N/A
J6: DF52-8S-0.8H_21_; DF528S08H21; Manufacturer_Part_Number DF52-8S-0.8H(21); Mouser Part Number 798-DF52-8S-0.8H21
J7, J8, J9: ERF8-005-05.0-L-DV-K-TR; SAMTEC_ERF8-005-05.0-L-DV-K-TR
LIDAR1: SM04B-GHE-TB; JST_GH_BM04B-GHS-TBT_1x04-1MP_P1.25mm_Vertical; Manufacturer_Part_Number SM04B-GHE-TB; Mouser Part Number 306-SM04BGHETBLFSN
R7, R8: 5.1k; R_0201_custom; Manufacturer_Part_Number ERJ-1GNF5101C; Mouser Part Number 667-ERJ-1GNF5101C
R9, R10, R42, R45: 22R; R_0201_0603Metric; Manufacturer_Part_Number ERJ-1GNF22R0C; Mouser Part Number 667-ERJ-1GNF22R0C
SWD1: SM04B-GHE-TB; JST_GH_BM04B; Manufacturer_Part_Number SM04B-GHE-TB; Mouser Part Number 306-SM04BGHETBLFSN
TOF1, TOF2, TOF3: SM04B-GHE-TB; JST_GH_BM04B; Manufacturer_Part_Number SM04B-GHE-TB; Mouser Part Number 306-SM04BGHETBLFSN
USBJUMP1: Conn_01x08_Pin; PinHeader_2x04_P1.27mm_Vertical_SMD

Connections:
4.5V: J5.6; also elsewhere on the board
+3.3V: J5.2, J6.1, TOF1.1, TOF2.1, TOF3.1; also elsewhere on the board
+5V: LIDAR1.4; also elsewhere on the board
/CONNECTOR/D+: D1.1 (I/O_1), J1.A6 (D+), J1.B6 (D+), R10.1
/CONNECTOR/D-: D1.3 (I/O_2), J1.A7 (D-), J1.B7 (D-), R9.1
/CONNECTOR/DATA+OUT: R10.2, USBJUMP1.2, USBJUMP1.6
/CONNECTOR/DATA-OUT: R9.2, USBJUMP1.4, USBJUMP1.8
/D+ESP32: USBJUMP1.5; also elsewhere on the board
/D+STM32: USBJUMP1.1; also elsewhere on the board
/D-ESP32: USBJUMP1.7; also elsewhere on the board
/D-STM32: USBJUMP1.3; also elsewhere on the board
/GPIO_MOT1: J7.03, J7.04; also elsewhere on the board
/GPIO_MOT2: J8.03, J8.04; also elsewhere on the board
/GPIO_MOT3: J9.03, J9.04; also elsewhere on the board
/HP+: J5.12; also elsewhere on the board
/HP-: J5.11; also elsewhere on the board
/LED_TIM: J5.8; also elsewhere on the board
/LIDAR_PWM: LIDAR1.1; also elsewhere on the board
/MOUSE_CLK: R42.2; also elsewhere on the board
/MOUSE_CS: J6.2; also elsewhere on the board
/MOUSE_INT: J6.8; also elsewhere on the board
/MOUSE_MISO: J6.5; also elsewhere on the board
/MOUSE_MOSI: R45.2; also elsewhere on the board
/NRST: SWD1.2; also elsewhere on the board
/RX_LIDAR: LIDAR1.3; also elsewhere on the board
/RX_MOT1: J7.05, J7.06; also elsewhere on the board
/RX_MOT2: J8.05, J8.06; also elsewhere on the board
/RX_MOT3: J9.05, J9.06; also elsewhere on the board
/RX_SUP: J5.10; also elsewhere on the board
/SCL_OLED: J5.4; also elsewhere on the board
/SCL_TOF1: TOF1.2; also elsewhere on the board
/SCL_TOF2: TOF2.2; also elsewhere on the board
/SCL_TOF3: TOF3.2; also elsewhere on the board
/SDA_OLED: J5.3; also elsewhere on the board
/SDA_TOF1: TOF1.3; also elsewhere on the board
/SDA_TOF2: TOF2.3; also elsewhere on the board
/SDA_TOF3: TOF3.3; also elsewhere on the board
/SWCLK: SWD1.3; also elsewhere on the board
/SWDIO: SWD1.4; also elsewhere on the board
/TX_MOT1: J7.07, J7.08; also elsewhere on the board
/TX_MOT2: J8.07, J8.08; also elsewhere on the board
/TX_MOT3: J9.07, J9.08; also elsewhere on the board
/TX_SUP: J5.9; also elsewhere on the board
GND: D1.2 (GND), H1.1, H2.1, H3.1, J1.A1 (GND), J1.A12 (GND), J1.B1 (GND), J1.B12 (GND), J1.S1 (SHIELD), J3.2, J3.3, J3.4, J5.1, J5.5, J5.7, J5.13 (MP1), J5.14 (MP2), J6.4, J6.6, J6.9, J6.10, J7.01, J7.02, J8.01, J8.02, J9.01, J9.02, LIDAR1.2, LIDAR1.MP, R7.2, R8.2, SWD1.1, SWD1.MP, TOF1.4, TOF1.MP, TOF2.4, TOF2.MP, TOF3.4, TOF3.MP; also elsewhere on the board
unnamed: J1.A5 (CC1), R7.1
unnamed: J1.B5 (CC2), R8.1
unnamed: J6.3, R42.1
unnamed: J6.7, R45.1
VBAT+: J3.1, J7.09, J7.10, J8.09, J8.10, J9.09, J9.10; also elsewhere on the board
VUSB: D1.5 (VDD), J1.A4 (VBUS), J1.A9 (VBUS), J1.B4 (VBUS), J1.B9 (VBUS); also elsewhere on the board

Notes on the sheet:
Batteries
TOF 2
LiDAR
ACCESSORIES
checker
USB data jumper
MOTOR 2
MOTOR 3
TOF 1
640-USB4110-GF-A
TOF 3
STM32 Prog
USB
MOTOR 1
ESD PROTECTION

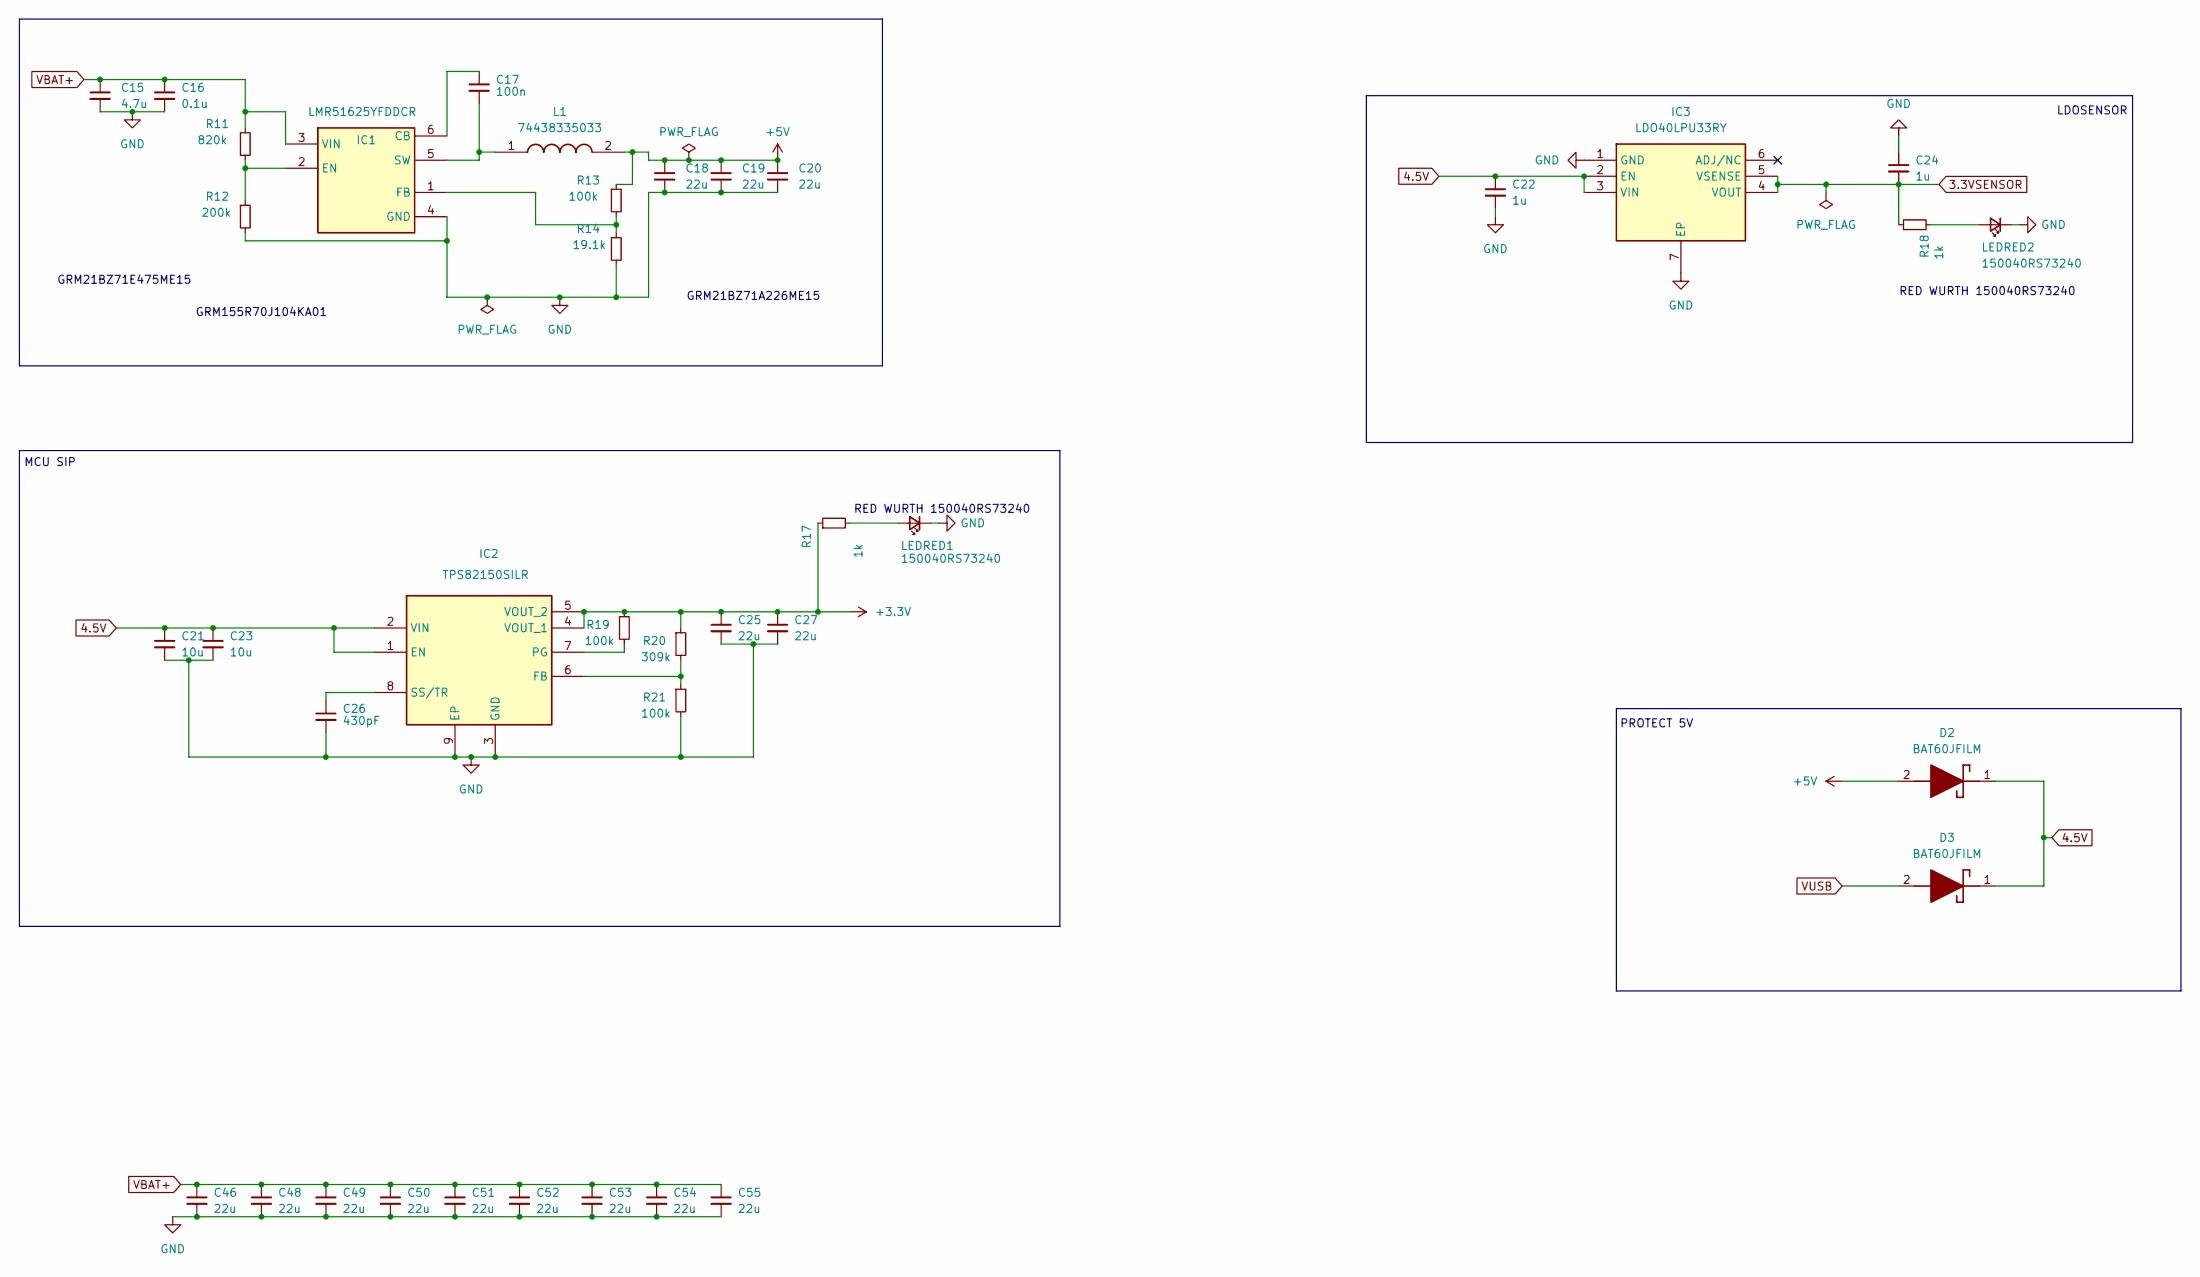
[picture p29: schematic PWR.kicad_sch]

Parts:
C15: 4.7u; C_0805_2012Metric
C16: 0.1u; C_0402_1005Metric
C17: 100n; C_0201_0603Metric
C18, C19, C20, C46, C48, C49, C50, C51, C52, C53, C54, C55: 22u; C_0805_2012Metric
C21, C23: 10u; C_0603_1608Metric; Manufacturer_Part_Number 885012105012; Mouser Part Number 710-885012105012
C22, C24: 1u; C_0402_1005Metric; Manufacturer_Part_Number 885012105012; Mouser Part Number 710-885012105012
C25, C27: 22u; C_0603_1608Metric; Manufacturer_Part_Number 885012105012; Mouser Part Number 710-885012105012
C26: 430pF; C_0201_0603Metric
D2, D3: BAT60JFILM; SOD2513X117N; Mouser Part Number 511-BAT60JFILM
IC1: LMR51625YFDDCR; SOT95P280X110-6N; Manufacturer_Part_Number LMR51625YFDDCR; Mouser Part Number 595-LMR51625YFDDCR
IC2: TPS82150SILR; TPS82130SILT; Manufacturer_Part_Number TPS82150SILR; Mouser Part Number 595-TPS82150SILR
IC3: LDO40LPU33RY; SON95P300X300X90-7N-D; Manufacturer_Part_Number LDO40LPU33RY; Mouser Part Number 511-LDO40LPU33RY
L1: 74438335033; INDC3030X150N; Manufacturer_Part_Number 74438335033; Mouser Part Number 710-74438335033
LEDRED1, LEDRED2: 150040RS73240; LED_0402_1005Metric; Manufacturer_Part_Number 150040RS73240; Mouser Part Number 710-150040RS73240
R11: 820k; R_0201_0603Metric
R12: 200k; R_0201_custom
R13, R19, R21: 100k; R_0201_0603Metric
R14: 19.1k; R_0201_custom
R17: 1k; R_0201_0603Metric; Manufacturer_Part_Number ERJ-1GNF1001C; Mouser Part Number 667-ERJ-1GNF1001C
R18: 1k; R_0201_custom; Manufacturer_Part_Number ERJ-1GNF1001C; Mouser Part Number 667-ERJ-1GNF1001C
R20: 309k; R_0201_0603Metric

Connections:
3.3VSENSOR: C24.2, IC3.4 (VOUT), IC3.5 (VSENSE), R18.1; also elsewhere on the board
4.5V: C21.1, C22.1, C23.1, D2.1 (K), D3.1 (K), IC2.1 (EN), IC2.2 (VIN), IC3.2 (EN), IC3.3 (VIN); also elsewhere on the board
+3.3V: C25.1, C27.1, IC2.4 (VOUT_1), IC2.5 (VOUT_2), R17.1, R19.1, R20.1; also elsewhere on the board
+5V: C18.1, C19.1, C20.1, D2.2 (A), L1.2, R13.1; also elsewhere on the board
GND: C15.2, C16.2, C18.2, C19.2, C20.2, C21.2, C22.2, C23.2, C24.1, C25.2, C26.2, C27.2, C46.2, C48.2, C49.2, C50.2, C51.2, C52.2, C53.2, C54.2, C55.2, IC1.4 (GND), IC2.3 (GND), IC2.9 (EP), IC3.1 (GND), IC3.7 (EP), LEDRED1.1 (K), LEDRED2.1 (K), R12.2, R14.2, R21.2; also elsewhere on the board
unnamed: C17.1, IC1.6 (CB)
unnamed: IC1.2 (EN), R11.2, R12.1
unnamed: IC1.1 (FB), R13.2, R14.1
unnamed: C17.2, IC1.5 (SW), L1.1
unnamed: IC2.6 (FB), R20.2, R21.1
unnamed: IC2.7 (PG), R19.2
unnamed: C26.1, IC2.8 (SS/TR)
unnamed: LEDRED1.2 (A), R17.2
unnamed: LEDRED2.2 (A), R18.2
VBAT+: C15.1, C16.1, C46.1, C48.1, C49.1, C50.1, C51.1, C52.1, C53.1, C54.1, C55.1, IC1.3 (VIN), R11.1; also elsewhere on the board
VUSB: D3.2 (A); also elsewhere on the board

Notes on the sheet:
GRM21BZ71E475ME15
GRM21BZ71A226ME15
RED WURTH 150040RS73240
LDOSENSOR
MCU SIP
PROTECT 5V
GRM155R70J104KA01

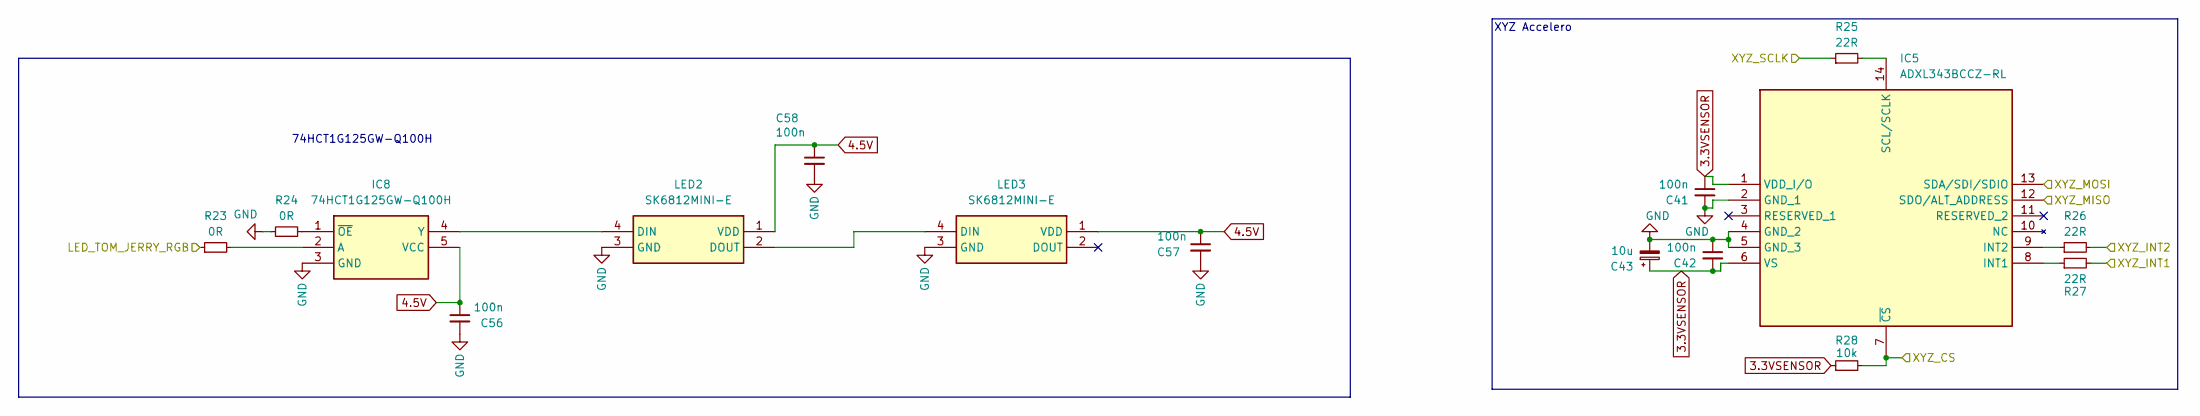
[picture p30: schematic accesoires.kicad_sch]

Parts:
C41: 100n; C_0201_0603Metric
C42, C56, C57, C58: 100n; C_0201_custom
C43: 10u; CP_EIA-1608-08_AVX-J
IC5: ADXL343BCCZ-RL; ADXL343BCCZRL; Manufacturer_Part_Number ADXL343BCCZ-RL; Mouser Part Number 584-ADXL343BCCZ-R
IC8: 74HCT1G125GW-Q100H; Manufacturer_Part_Number 74HCT1G125GW-Q100H; Mouser Part Number 77174HCT1G125GWQ100H
LED2, LED3: SK6812MINI-E; SK6812MINIE; Manufacturer_Part_Number SK6812MINI-E
R23, R24: 0R; R_0201_custom; Manufacturer_Part_Number ERJ-1GNF1000C; Mouser Part Number 667-ERJ-1GNF1000C
R25: 22R; R_0201_custom; Manufacturer_Part_Number ERJ-1GNF1000C; Mouser Part Number 667-ERJ-1GNF1000C
R26, R27: 22R; R_0201_0603Metric; Manufacturer_Part_Number ERJ-1GNF1000C; Mouser Part Number 667-ERJ-1GNF1000C
R28: 10k; R_0201_0603Metric; Manufacturer_Part_Number ERJ-1GNF1000C; Mouser Part Number 667-ERJ-1GNF1000C

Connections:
3.3VSENSOR: C41.1, C42.2, C43.1, IC5.1 (VDD_I/O), IC5.6 (VS), R28.1; also elsewhere on the board
4.5V: C56.1, C57.1, C58.1, IC8.5 (VCC), LED2.1 (VDD), LED3.1 (VDD); also elsewhere on the board
/ACCEL_CLK: R25.1; also elsewhere on the board
/ACCEL_CS: IC5.7 (~CS), R28.2; also elsewhere on the board
/ACCEL_INT1: R27.2; also elsewhere on the board
/ACCEL_INT2: R26.2; also elsewhere on the board
/ACCEL_MISO: IC5.12 (SDO/ALT_ADDRESS); also elsewhere on the board
/ACCEL_MOSI: IC5.13 (SDA/SDI/SDIO); also elsewhere on the board
/RGB_TOM_JERRY: R23.1; also elsewhere on the board
GND: C41.2, C42.1, C43.2, C56.2, C57.2, C58.2, IC5.2 (GND_1), IC5.4 (GND_2), IC5.5 (GND_3), IC8.3 (GND), LED2.3 (GND), LED3.3 (GND), R24.1; also elsewhere on the board
unnamed: IC5.8 (INT1), R27.1
unnamed: IC5.9 (INT2), R26.1
unnamed: IC5.14 (SCL/SCLK), R25.2
unnamed: IC8.2 (A), R23.2
unnamed: IC8.4 (Y), LED2.4 (DIN)
unnamed: IC8.1 (~OE), R24.2
unnamed: LED2.2 (DOUT), LED3.4 (DIN)

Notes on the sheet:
XYZ Accelero
74HCT1G125GW-Q100H

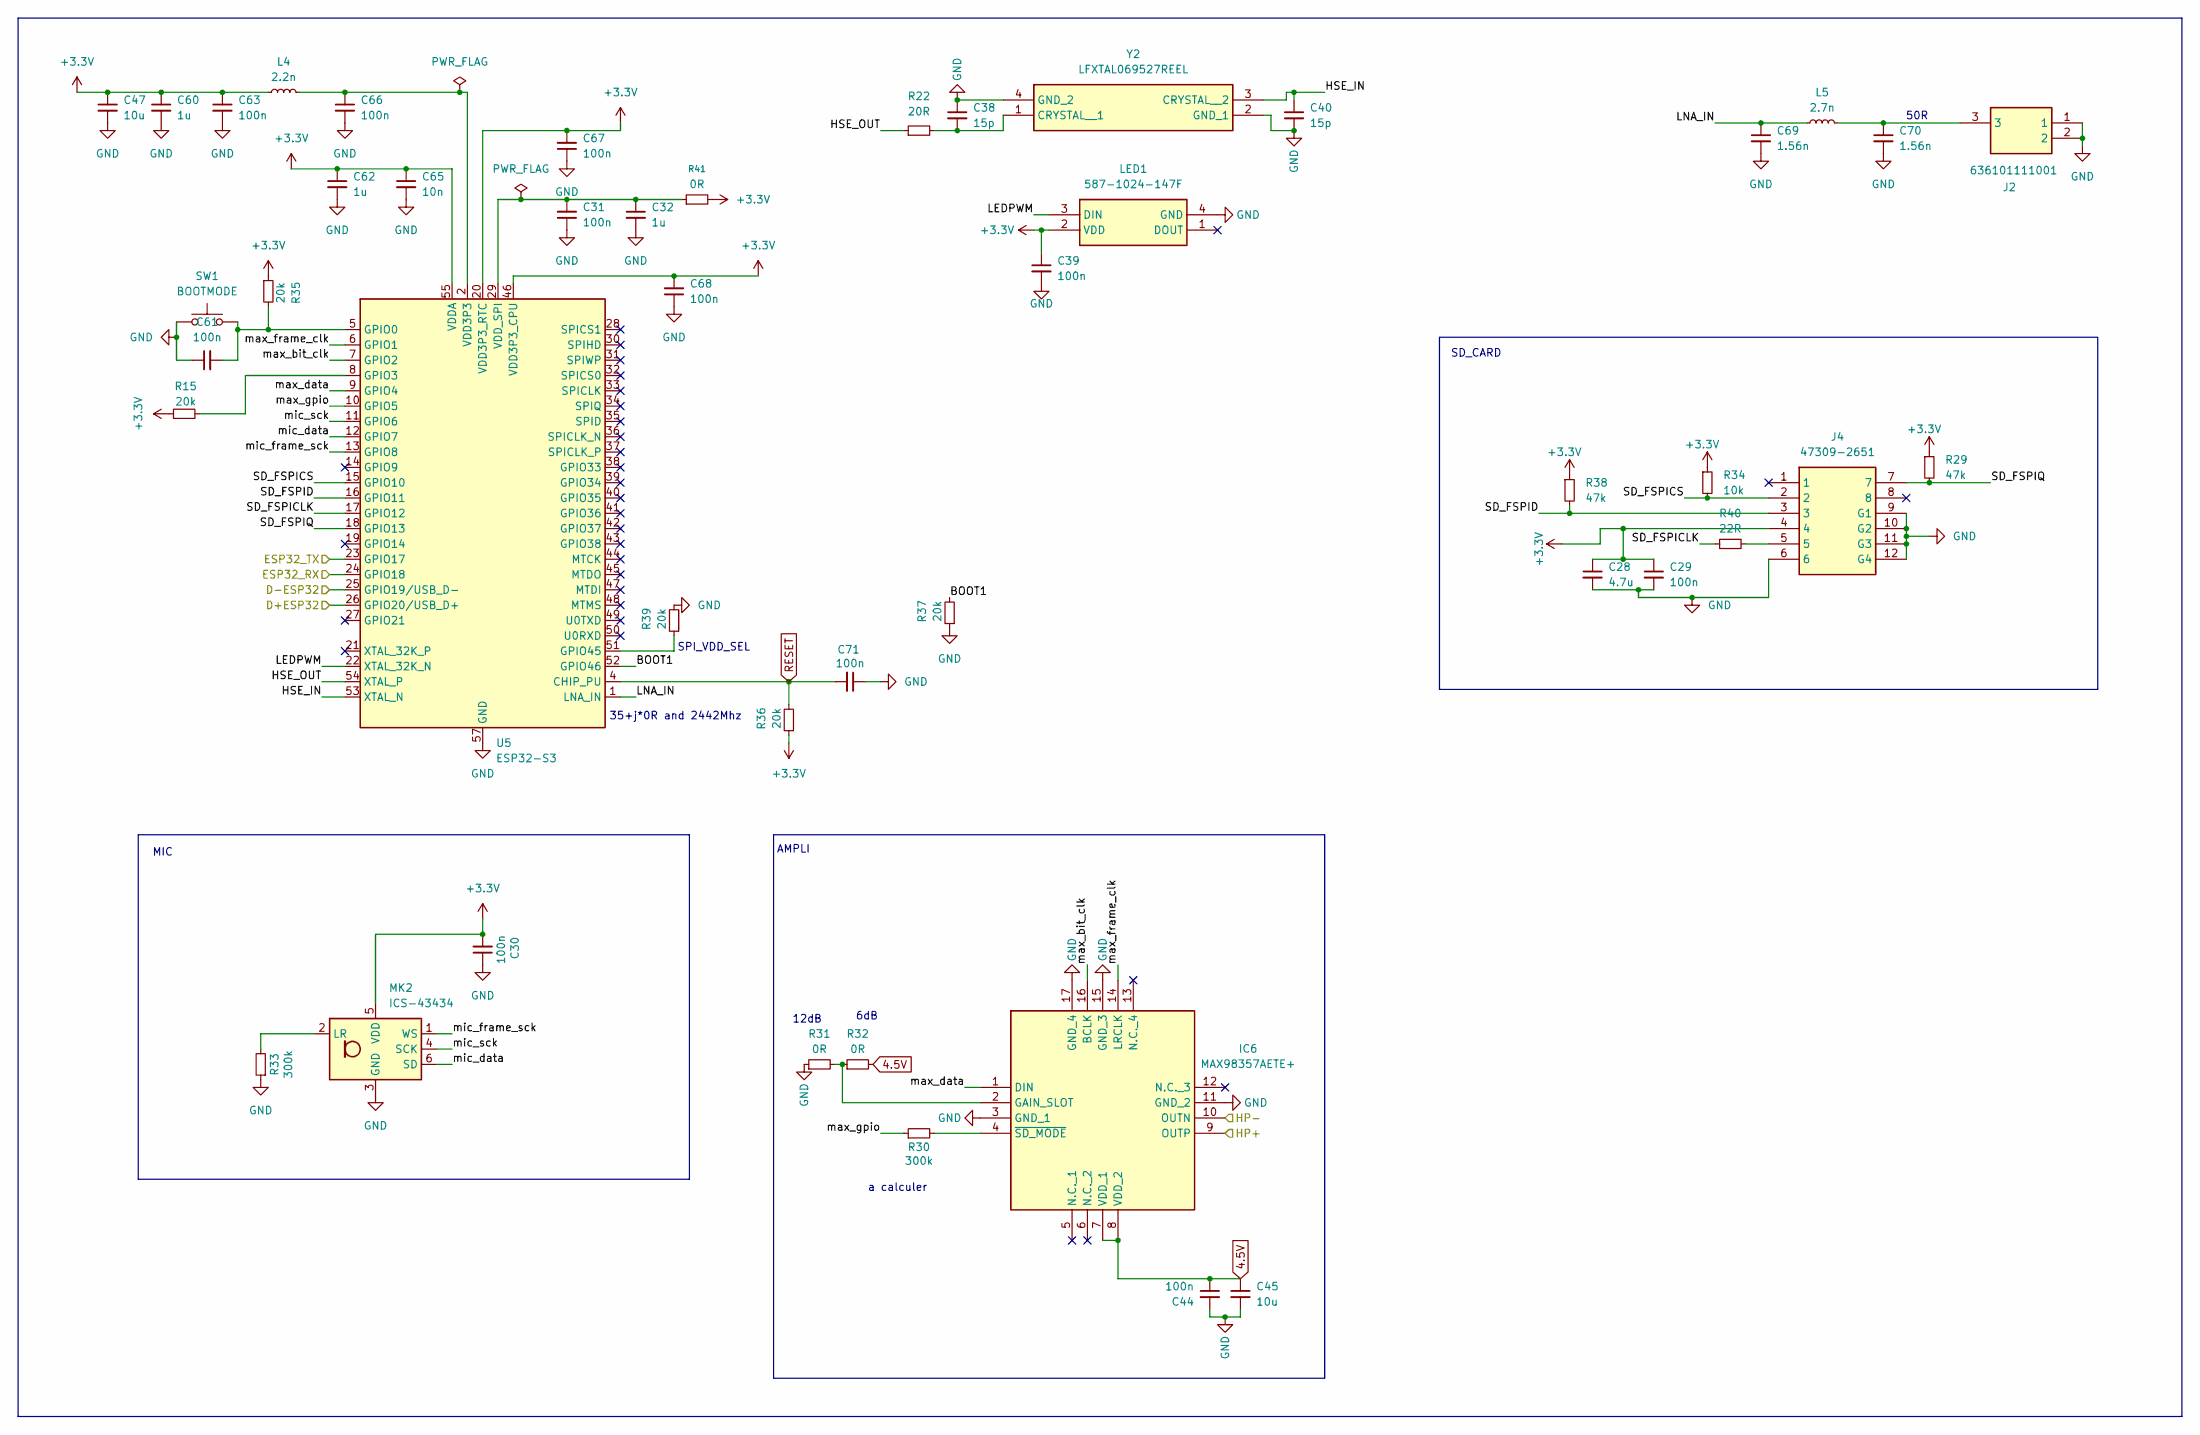
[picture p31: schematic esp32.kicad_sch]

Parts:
C28: 4.7u; C_0402_1005Metric_Pad0.74x0.62mm_HandSolder
C29, C39, C44: 100n; C_0201_0603Metric
C30, C31, C61, C63, C66, C67, C68, C71: 100n; C_0201_0603Metric_Pad0.64x0.40mm_HandSolder
C32, C60, C62: 1u; C_0402_1005Metric_Pad0.74x0.62mm_HandSolder
C38, C40: 15p; C_0201_custom
C45: 10u; C_0402_1005Metric; Manufacturer_Part_Number 885012105008; Mouser Part Number 710-885012105008
C47: 10u; C_0402_1005Metric_Pad0.74x0.62mm_HandSolder
C65: 10n; C_0201_0603Metric_Pad0.64x0.40mm_HandSolder
C69, C70: 1.56n; C_0402_1005Metric_Pad0.74x0.62mm_HandSolder
IC6: MAX98357AETE+; QFN50P300X300X80-17N; Manufacturer_Part_Number MAX98357AETE+; Mouser Part Number 700-MAX98357AETE+
J2: 636101111001; Mouser Part Number 710-636101111001
J4: 47309-2651; 473092651; Manufacturer_Part_Number 47309-2651
L4: 2.2n; L_0603_1608Metric
L5: 2.7n; L_0603_1608Metric
LED1: 587-1024-147F; 5871024147F; Manufacturer_Part_Number 587-1024-147F
MK2: ICS-43434; InvenSense_ICS-43434-6_3.5x2.65mm
R15, R35, R36, R37, R39: 20k; R_0201_0603Metric_Pad0.64x0.40mm_HandSolder
R22: 20R; R_0201_0603Metric
R29, R38: 47k; R_0201_0603Metric
R30, R33: 300k; R_0201_0603Metric; Manufacturer_Part_Number ERJ-1GNF1000C; Mouser Part Number 667-ERJ-1GNF1000C
R31: 0R; R_0201_custom; Manufacturer_Part_Number ERJ-1GNF1000C; Mouser Part Number 667-ERJ-1GNF1000C
R32: 0R; R_0201_0603Metric; Manufacturer_Part_Number ERJ-1GNF1000C; Mouser Part Number 667-ERJ-1GNF1000C
R34: 10k; R_0201_0603Metric
R40: 22R; R_0201_0603Metric
R41: 0R; R_0402_1005Metric_Pad0.72x0.64mm_HandSolder
SW1: BOOTMODE; KXT341LHS
U5: ESP32-S3; QFN-56-1EP_7x7mm_P0.4mm_EP4x4mm
Y2: LFXTAL069527REEL; Manufacturer_Part_Number LFXTAL069527REEL

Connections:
4.5V: C44.1, C45.1, IC6.7 (VDD_1), IC6.8 (VDD_2), R32.2; also elsewhere on the board
+3.3V: C28.1, C29.1, C30.2, C39.1, C47.1, C60.1, C62.1, C63.1, C65.1, C67.2, C68.2, J4.4, L4.1, LED1.2 (VDD), MK2.5 (VDD), R15.1, R29.1, R34.1, R35.1, R36.1, R38.1, R41.2, U5.20 (VDD3P3_RTC), U5.46 (VDD3P3_CPU), U5.55 (VDDA), U5.56 (VDDA); also elsewhere on the board
/D+ESP32: U5.26 (GPIO20/USB_D+); also elsewhere on the board
/D-ESP32: U5.25 (GPIO19/USB_D-); also elsewhere on the board
/ESP32/BOOT1: R37.2, U5.52 (GPIO46)
/ESP32/HSE_IN: C40.1, U5.53 (XTAL_N), Y2.3 (CRYSTAL__2)
/ESP32/HSE_OUT: R22.1, U5.54 (XTAL_P)
/ESP32/LEDPWM: LED1.3 (DIN), U5.22 (XTAL_32K_N)
/ESP32/LNA_IN: C69.1, L5.1, U5.1 (LNA_IN)
/ESP32/SD_FSPICLK: R40.1, U5.17 (GPIO12)
/ESP32/SD_FSPICS: J4.2, R34.2, U5.15 (GPIO10)
/ESP32/SD_FSPID: J4.3, R38.2, U5.16 (GPIO11)
/ESP32/SD_FSPIQ: J4.7, R29.2, U5.18 (GPIO13)
/ESP32/max_bit_clk: IC6.16 (BCLK), U5.7 (GPIO2)
/ESP32/max_data: IC6.1 (DIN), U5.9 (GPIO4)
/ESP32/max_frame_clk: IC6.14 (LRCLK), U5.6 (GPIO1)
/ESP32/max_gpio: R30.1, U5.10 (GPIO5)
/ESP32/mic_data: MK2.6 (SD), U5.12 (GPIO7)
/ESP32/mic_frame_sck: MK2.1 (WS), U5.13 (GPIO8)
/ESP32/mic_sck: MK2.4 (SCK), U5.11 (GPIO6)
/ESP32_RX: U5.24 (GPIO18); also elsewhere on the board
/ESP32_TX: U5.23 (GPIO17); also elsewhere on the board
/HP+: IC6.9 (OUTP); also elsewhere on the board
/HP-: IC6.10 (OUTN); also elsewhere on the board
GND: C28.2, C29.2, C30.1, C31.1, C32.2, C38.1, C39.2, C40.2, C44.2, C45.2, C47.2, C60.2, C61.1, C62.2, C63.2, C65.2, C66.2, C67.1, C68.1, C69.2, C70.2, C71.1, IC6.3 (GND_1), IC6.11 (GND_2), IC6.15 (GND_3), IC6.17 (GND_4), J2.1, J2.2, J4.6, J4.9 (G1), J4.10 (G2), J4.11 (G3), J4.12 (G4), LED1.4 (GND), MK2.3 (GND), R31.1, R33.1, R37.1, R39.2, SW1.1, U5.57 (GND), Y2.2 (GND_1), Y2.4 (GND_2); also elsewhere on the board
unnamed: C66.1, L4.2, U5.2 (VDD3P3), U5.3 (VDD3P3)
unnamed: C70.1, J2.3, L5.2
unnamed: IC6.2 (GAIN_SLOT), R31.2, R32.1
unnamed: IC6.4 (~SD_MODE), R30.2
unnamed: J4.5, R40.2
unnamed: MK2.2 (LR), R33.2
unnamed: C61.2, R35.2, SW1.2, U5.5 (GPIO0)
unnamed: R15.2, U5.8 (GPIO3)
unnamed: R39.1, U5.51 (GPIO45)
unnamed: C31.2, C32.1, R41.1, U5.29 (VDD_SPI)
unnamed: C38.2, R22.2, Y2.1 (CRYSTAL__1)
RESET: C71.2, R36.2, U5.4 (CHIP_PU)

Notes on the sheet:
50R
6dB
a calculer
12dB
MIC
35+j*0R and 2442Mhz
SD_CARD
AMPLI
SPI_VDD_SEL

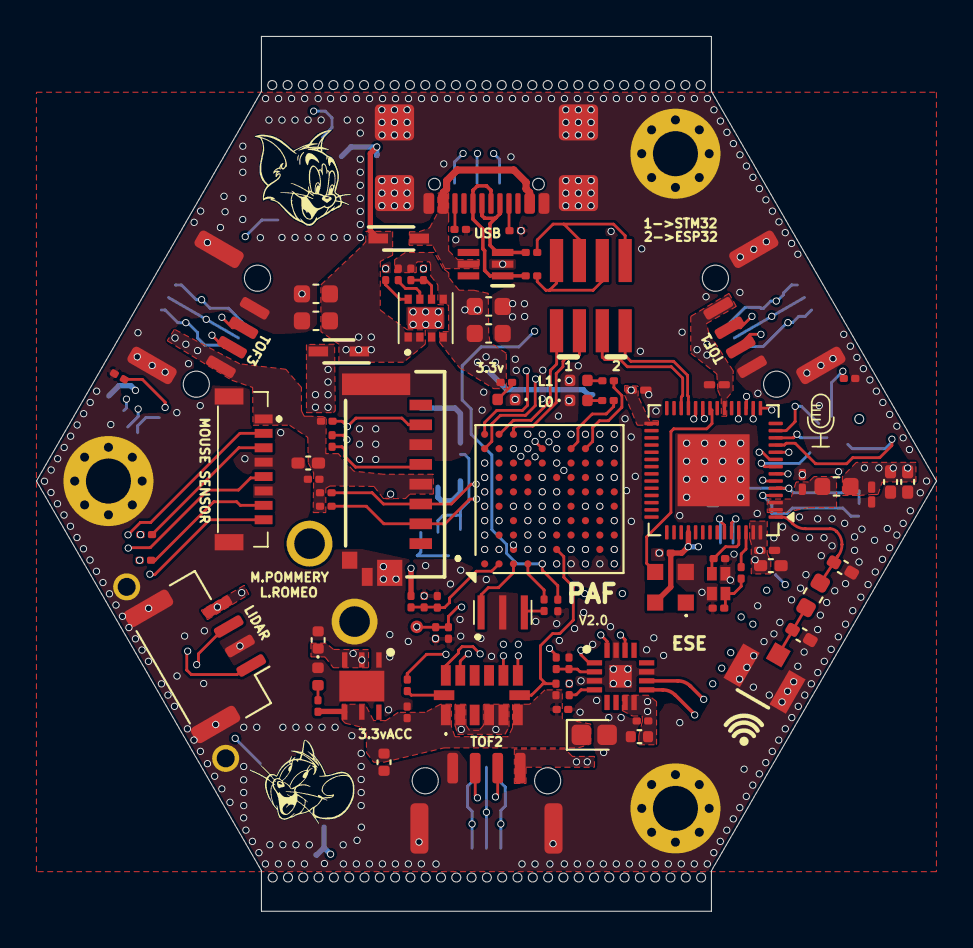
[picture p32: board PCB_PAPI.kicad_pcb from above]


Board: 8 copper layers, 50.0 x 48.6 mm, 150 parts (60 on the bottom side), 115 nets.

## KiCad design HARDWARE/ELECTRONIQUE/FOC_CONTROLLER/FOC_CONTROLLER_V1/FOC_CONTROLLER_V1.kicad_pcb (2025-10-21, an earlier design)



Board: 8 copper layers, 34.4 x 34.9 mm, 113 parts (23 on the bottom side), 71 nets.

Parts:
C1, C6, C9, C12, C28, C29: 100n; C_0201_0603Metric_Pad0.64x0.40mm_HandSolder
C2, C3, C4, C13, C17, C20: 1u; C_0603_1608Metric
C5: 4.7u; C_0402_1005Metric
C7: 47u; C_0805_2012Metric
C8: 10n; C_0201_0603Metric_Pad0.64x0.40mm_HandSolder
C10: 220n; C_0603_1608Metric
C11: 10u; C_0603_1608Metric
C14, C16, C19: DNP; C_0201_0603Metric_Pad0.64x0.40mm_HandSolder
C15, C18, C21: 470p; C_0201_0603Metric_Pad0.64x0.40mm_HandSolder
C22: 1u; C_0402_1005Metric
C23, C24, C25, C26, C27, C31, C33, C34, C35, C36: 22u; C_0805_2012Metric
C30: 1nF; C_0201_0603Metric_Pad0.64x0.40mm_HandSolder
D1: STPS0560Z
D2, D3, D4, D5, D6, D7: BAS16LP-7B; D_01005_0402Metric_Pad0.57x0.30mm_HandSolder
D8: LED; LED_0402_1005Metric
IC1: STSPIN32G0A2; QFN50P700X700X105-49N-D
IC2: MA330GQ-Z; QFN50P300X300X100-17N-D
J1, J2: SM06B-GHS-TB_LF__SN_; SM06B-GHS-TB
L2: 74438335220
Q1, Q2, Q3: DMT6018LDR-7; DMT6018LDR7
R1, R2, R40: 10k; R_0201_0603Metric_Pad0.64x0.40mm_HandSolder
R3, R4, R7, R20, R21, R31, R32, R38, R39: 0R; R_0201_0603Metric_Pad0.64x0.40mm_HandSolder
R5, R6, R18, R19, R29, R30: 120R; R_0201_0603Metric_Pad0.64x0.40mm_HandSolder
R9, R10, R15, R22, R26, R33, R47: 1k; R_0201_0603Metric_Pad0.64x0.40mm_HandSolder
R11, R12, R16, R17, R27, R28, R42: 15k; R_0201_0603Metric_Pad0.64x0.40mm_HandSolder
R13, R23, R34: 7.5k; R_0201_0603Metric_Pad0.64x0.40mm_HandSolder
R14, R25, R36: 220R; R_0201_0603Metric_Pad0.64x0.40mm_HandSolder
R37: 100R; R_0201_0603Metric_Pad0.64x0.40mm_HandSolder
R41: 100k; R_0201_0603Metric_Pad0.64x0.40mm_HandSolder
R43, R44, R45: 2.2k; R_0201_0603Metric_Pad0.64x0.40mm_HandSolder
R46: 18k; R_0201_0603Metric_Pad0.64x0.40mm_HandSolder
R48, R49, R50: R_Shunt; 4wire_0603
S1: 435151014824
TP1, TP1#2, TP1#3, TP1#4: TestPoint; m3test
TP5, TP6, TP7: TestPoint; hole_1.5mm
TP8, TP9, TP10, TP11, TP12, TP13, TP15: TestPoint; pad_0.7mm

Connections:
+3.3V: C1.1, C5.1, C6.1, C7.1, C22.1, IC1.5 (VDD), IC1.9 (REG3V3), IC2.13 (VDD), J1.4, L2.1, R1.2, R2.1, R12.1, R16.1, R27.1, R40.1, R41.1, R46.1
/BTN: C28.1, IC1.39 (PA12_[PA10]), J1.6, R40.2
/HSU: D2.1 (K), IC1.34 (HSU), R5.1
/HSV: D4.1 (K), IC1.30 (HSV), R18.1
/HSW: D6.1 (K), IC1.26 (HSW), R29.1
/ISNSU: C18.2, IC1.20 (PA7), R25.2
/ISNSV: C21.2, IC1.18 (PA6), R36.2
/ISNSW: C15.2, IC1.21 (PB1), R14.2
/LSU: D3.1 (K), IC1.37 (LSU), R6.1
/LSV: D5.1 (K), IC1.33 (LSV), R19.1
/LSW: D7.1 (K), IC1.29 (LSW), R30.1
/MGH: IC1.13 (PA1), R39.2, TP12.1
/MGL: IC1.16 (PA4), R38.1, TP11.1
/NRST: C9.1, J1.1, R3.2, S1.1 (NO_1), S1.2 (NO_2)
/OP1N: C14.1, IC1.23 (OP1N), R9.2, R13.1
/OP1O: C14.2, IC1.22 (OP1O), R13.2, R14.1
/OP1P: IC1.24 (OP1P), R10.2, R11.1, R12.2
/OP2N: C16.1, IC1.3 (OP2N), R22.2, R23.1, TP9.1
/OP2O: C16.2, IC1.4 (OP2O), R23.2, R25.1, TP8.1
/OP2P: IC1.2 (OP2P), R15.2, R16.2, R17.1, TP10.1
/OP3N: C19.1, IC1.47 (OP3N), R33.2, R34.1
/OP3O: C19.2, IC1.48 (OP3O), R34.2, R36.1
/OP3P: IC1.46 (OP3P), R26.2, R27.2, R28.1
/OUTU: C2.2, IC1.35 (OUTU), Q1.2 (S1), Q1.6 (D2), TP5.1
/OUTV: C3.2, IC1.31 (OUTV), Q2.2 (S1), Q2.6 (D2), TP6.1
/OUTW: C4.2, IC1.27 (OUTW), Q3.2 (S1), Q3.6 (D2), TP7.1
/REG12: C11.2, C12.1, IC1.6 (REG12)
/SHUNT+AFTER: C30.1, IC1.25 (OCCOMP), R43.2, R44.2, R45.2, R46.2
/SHUNT+U: R15.1, R43.1, R48.2
/SHUNT+V: R26.1, R44.1, R49.2
/SHUNT+W: R10.1, R45.1, R50.2
/SHUNT-U: R22.1, R48.3
/SHUNT-V: R33.1, R49.3
/SHUNT-W: R9.1, R50.3
/SPI2_CS: IC1.42 (PA15), IC2.5 (CS), R1.1
/SPI2_MISO: IC1.43 (PB6), IC2.7 (MISO)
/SPI2_MOSI: IC1.45 (PB7), IC2.4 (MOSI), TP13.1
/SPI2_SCK: IC1.12 (PA0), R37.1
/SW: D1.1 (K), IC1.8 (SW), L2.2
/SWCLK: IC1.41 (PA14-BOOT0), J1.2
/SWDIO: IC1.40 (PA13), J1.3
/UART_RX: IC1.15 (PA3), J2.3
/UART_TX: IC1.14 (PA2), J2.4
GND: C1.2, C5.2, C6.2, C7.2, C8.2, C9.2, C10.1, C11.1, C12.2, C13.1, C15.1, C17.1, C18.1, C20.1, C21.1, C22.2, C23.2, C24.2, C25.2, C26.2, C27.2, C28.2, C29.2, C30.2, C31.2, C33.2, C34.2, C35.2, C36.2, D1.2 (A), IC1.19 (TESTMODE), IC1.44 (GND_1), IC1.49 (GND_2), IC2.8 (GND), IC2.10 (TEST), IC2.17 (EP), J1.5, J1.7, J1.8, J2.5, J2.6, J2.7, J2.8, R11.2, R17.2, R28.2, R42.2, R47.1, R48.4, R49.4, R50.4, S1.3 (COM_1), S1.4 (COM_2), S1.5 (GND_1), S1.6 (GND_2), TP1.1, TP1#2.1, TP1#3.1, TP1#4.1, TP15.1
unnamed: D2.2 (A), R4.1
unnamed: D3.2 (A), R7.1
unnamed: D4.2 (A), R20.1
unnamed: D5.2 (A), R21.1
unnamed: D6.2 (A), R31.1
unnamed: D7.2 (A), R32.1
unnamed: D8.2 (A), IC1.10 (PF0-OSC_IN)
unnamed: D8.1 (K), R47.2
unnamed: C8.1, IC1.38 (NSTBY), R2.2
unnamed: C29.1, IC1.17 (PA5), R41.2, R42.1
unnamed: IC1.11 (PF2-NRST), R3.1
unnamed: C2.1, IC1.36 (VBOOTU)
unnamed: C3.1, IC1.32 (VBOOTV)
unnamed: C4.1, IC1.28 (VBOOTW)
unnamed: IC2.16 (MGH), R39.1
unnamed: IC2.11 (MGL), R38.2
unnamed: IC2.12 (SCLK), R37.2
unnamed: Q1.1 (G1), R4.2, R5.2
unnamed: Q1.4 (G2), R6.2, R7.2
unnamed: Q1.3 (S2), R48.1
unnamed: Q2.1 (G1), R18.2, R20.2
unnamed: Q2.4 (G2), R19.2, R21.2
unnamed: Q2.3 (S2), R49.1
unnamed: Q3.1 (G1), R29.2, R31.2
unnamed: Q3.4 (G2), R30.2, R32.2
unnamed: Q3.3 (S2), R50.1
VBAT+: C10.2, C13.2, C17.2, C20.2, C23.1, C24.1, C25.1, C26.1, C27.1, C31.1, C33.1, C34.1, C35.1, C36.1, IC1.7 (VM), J2.1, J2.2, Q1.5 (D1), Q2.5 (D1), Q3.5 (D1)

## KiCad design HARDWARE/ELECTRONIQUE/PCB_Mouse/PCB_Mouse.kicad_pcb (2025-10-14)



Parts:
C1: 4.7uF/10V; C_0603_1608Metric_Pad1.08x0.95mm_HandSolder
C2: 100nF; C_0402_1005Metric
C3, C4, C5, C8, C10, C14: 1u; C_0402_1005Metric
C6: 0.1u; C_0402_1005Metric
C7: 10n; C_0402_1005Metric
C9, C15, C16, C17: 100n; C_0402_1005Metric
C11: 4.7u; C_0402_1005Metric
C12, C13: 16p; C_0402_1005Metric
D3: LED; LED_0402_1005Metric
H1, H2, H3, H4: MountingHole_Pad; MountingHole_2.2mm_M2_ISO14580_Pad
IC1, IC2: LDLN025M33R; SOT95P280X145-5N; Manufacturer_Part_Number LDLN025M33R; Mouser Part Number 511-LDLN025M33R
J1, J2: SM04B-GHS-TB_LF__SN_; SM04B-GHS-TB; Manufacturer_Part_Number SM04B-GHS-TB(LF)(SN); Mouser Part Number N/A
R1: 10k; R_0402_1005Metric; not fitted
R2, R5: 10k; R_0402_1005Metric
R3: 39R; R_0402_1005Metric
R4: 0R; R_0402_1005Metric
R20: 1.1k; R_0402_1005Metric
SW1: RSTBTN; KXT341LHS
U1: PMW3360
U2: STM32G431CBUx; QFN-48-1EP_7x7mm_P0.5mm_EP5.6x5.6mm
Y1: Crystal_GND24_Small; LFXTAL069527REEL

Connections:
+1V8: C5.1, IC2.5 (OUT), R3.1, U1.4 (VDD)
+3.3V: C4.1, C7.2, C8.2, C9.2, C10.2, C11.1, C15.2, C16.2, C17.2, IC1.5 (OUT), R1.1, R2.1, U1.5 (VDDIO), U2.1 (VBAT), U2.20 (VREF+), U2.21 (VDDA), U2.23 (VDD), U2.35 (VDD), U2.48 (VDD)
/CS: U1.13 (~CS), U2.12 (PA4)
/MISO: R2.2, U1.12 (MISO), U2.14 (PA6)
/MOSI: U1.11 (MOSI), U2.15 (PA7)
/NRST: C6.2, J1.2, SW1.2, U2.7 (PG10)
/RESET: R1.2, U1.7 (~RESET), U2.43 (PB5)
/SCLK: R5.2, U2.13 (PA5)
/SENSOR_INT: R4.2, U2.16 (PC4)
/SWCLK: J1.4, U2.37 (PA14)
/SWDIO: J1.3, U2.36 (PA13)
/USART1_RX: J2.3, U2.45 (PB7)
/USART1_TX: J2.2, U2.44 (PB6)
GND: C1.2, C2.2, C3.2, C4.2, C5.2, C6.1, C7.1, C8.1, C9.1, C10.1, C11.2, C12.2, C13.1, C14.2, C15.1, C16.1, C17.1, H1.1, H2.1, H3.1, H4.1, IC1.2 (GND), IC2.2 (GND), J1.1, J2.1, R20.1, SW1.1, U1.8 (GND), U2.49 (VSS), Y1.2, Y1.4
unnamed: D3.2 (A), U2.27 (PB14)
unnamed: D3.1 (K), R20.2
unnamed: R3.2, U1.15 (LED_P)
unnamed: R4.1, U1.9 (MOTION)
unnamed: R5.1, U1.10 (SCLK)
unnamed: C1.1, C2.1, U1.3 (VDDPIX)
unnamed: C13.2, U2.5 (PF0), Y1.1
unnamed: C12.1, U2.6 (PF1), Y1.3
VDD: C3.1, C14.1, IC1.1 (IN), IC1.3 (EN), IC2.1 (IN), IC2.3 (EN), J2.4

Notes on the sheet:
Reserved, ~{RESET} pin has a built in weak pull up circuit.
CONTROLEUR PRINCIPAL
Mounting Holes


Board: 2 copper layers, 38.4 x 28.3 mm, 36 parts (0 on the bottom side), 23 nets.

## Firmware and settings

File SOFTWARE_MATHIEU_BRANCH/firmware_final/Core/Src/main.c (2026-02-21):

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
/* Includes ------------------------------------------------------------------*/
#include "main.h"
#include "cmsis_os.h"
#include "dma.h"
#include "i2c.h"
#include "spi.h"
#include "tim.h"
#include "usart.h"
#include "usb_device.h"
#include "gpio.h"

/* USER CODE BEGIN Includes */
#include "adxl343.h"
#include "ssd1306.h"
#include "led.h"
#include "mcc_com_master.h"
#include "odometry.h"
#include "vl53l0x.h"
#include "lidar.h"
#include "crsf.h"
/* USER CODE END Includes */


/* USER CODE BEGIN PV */
adxl343_t adxldata;
MOTOR_COM com_struct;
Lidar_t lidar_struct;
ODOM_struct odom_struct;

led_strip_t tomandjerry;
led_strip_t extled;
VL53L0X_t tof_array[3];

CRSF_t crsf_struct;

extern uint8_t  tomjerry_grb[WS2812_GRB_BUF_LEN(TOM_JERRY_LED_COUNT)];
extern uint32_t tomjerry_dma[WS2812_DMA_BUF_LEN(TOM_JERRY_LED_COUNT)];



/* USER CODE END PV */

void SystemClock_Config(void);
static void MPU_Config(void);
void MX_FREERTOS_Init(void);
/* USER CODE BEGIN 0 */
void HAL_GPIO_EXTI_Callback(uint16_t GPIO_Pin){

	if(GPIO_Pin == GPIO_PIN_0){
		ADXL343_INT_HANDLER(&adxldata, 100);
		#define ADXL343_DEBOUNCE_MS  120u
		static uint32_t last_irq_ms = 0;
		uint32_t now = HAL_GetTick();
		if ((uint32_t)(now - last_irq_ms) < ADXL343_DEBOUNCE_MS) {
			return;
		}
		last_irq_ms = now;
		adxldata.filtered_tap_event=1;
 }
}

void HAL_TIM_PWM_PulseFinishedCallback(TIM_HandleTypeDef *htim){
	if(htim->Instance==TIM1){
	LED_Strip_DMA_Callback(&tomandjerry);
	}
	else if(htim->Instance==TIM3){
	LED_Strip_DMA_Callback(&extled);
	}
	else{

	}
}


void HAL_UART_RxHalfCpltCallback(UART_HandleTypeDef *huart)
{
    if (huart->Instance == USART1)
    {
#ifdef NORMAL_MODE
        com_struct.write_index = (uint16_t)(MOTOR_COM_RX_BUF_SIZE / 2u);
#endif
#ifdef DEBUG_MODE
        (void)CDC_Transmit_FS(&com_struct.dbg_rx_buf[0], DEBUG_RX_BUF_SIZE / 2u);
#endif
    }
    if (huart->Instance == UART8)
    {
    	lidar_struct.parse_struct.ylidar_write_index=YLIDAR_CIRC_BUF_SIZE/2u;
    }
    if (huart->Instance == USART3)
    {
    	crsf_struct.crsf_write_index=CRSF_CIRC_BUF_LENGHT/2u;
    }
}


void HAL_UART_RxCpltCallback(UART_HandleTypeDef *huart)
{
    if (huart->Instance == USART1)
    {
#ifdef NORMAL_MODE
        com_struct.write_index = 0;
#endif
#ifdef DEBUG_MODE
        (void)CDC_Transmit_FS(&com_struct.dbg_rx_buf[DEBUG_RX_BUF_SIZE / 2u],
                              DEBUG_RX_BUF_SIZE / 2u);
#endif
    }
    if (huart->Instance == UART8)
    {
    	lidar_struct.parse_struct.ylidar_write_index=0;
    }
    if (huart->Instance == USART3)
    {
    	crsf_struct.crsf_write_index=0u;
    }
}

/* USER CODE END 0 */

/**
  * @brief  The application entry point.
  * @retval int
  */
int main(void)
{

  /* MPU Configuration--------------------------------------------------------*/
  MPU_Config();

  /* MCU Configuration--------------------------------------------------------*/

  /* Reset of all peripherals, Initializes the Flash interface and the Systick. */
  HAL_Init();

  /* Configure the system clock */
  SystemClock_Config();

  /* Initialize all configured peripherals */
  MX_GPIO_Init();
  MX_DMA_Init();
  MX_SPI4_Init();
  MX_TIM1_Init();
  MX_USART1_UART_Init();
  MX_I2C1_Init();
  MX_I2C3_Init();
  MX_I2C4_Init();
  MX_UART8_Init();
  MX_USART3_UART_Init();
  MX_TIM3_Init();
  /* USER CODE BEGIN 2 */

  CoreDebug->DEMCR |= CoreDebug_DEMCR_TRCENA_Msk;
  DWT->CYCCNT = 0;
  DWT->CTRL |= DWT_CTRL_CYCCNTENA_Msk;

  crsf_Init(&crsf_struct,&huart3);

  MotorCom_Init(&com_struct,&huart1);

  ADXL343_Init(&adxldata, &hspi4, ACCEL_CS_GPIO_Port, ACCEL_CS_Pin,ADXL343_BW_RATE_VALUE, ADXL343_DATA_FMT_RANGE_4G,100);

  Lidar_Init(&lidar_struct,&huart8,LIDAR_SPEED_GPIO_Port, LIDAR_SPEED_Pin);


  /* USER CODE END 2 */

  /* Call init function for freertos objects (in cmsis_os2.c) */
  MX_FREERTOS_Init();

  /* Start scheduler */
  osKernelStart();

  /* We should never get here as control is now taken by the scheduler */

  /* Infinite loop */
  /* USER CODE BEGIN WHILE */
  while (1)
  {
    /* USER CODE END WHILE */

    /* USER CODE BEGIN 3 */
  }
  /* USER CODE END 3 */
}

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
 /* MPU Configuration */

void MPU_Config(void)
{
  MPU_Region_InitTypeDef MPU_InitStruct = {0};

  /* Disables the MPU */
  HAL_MPU_Disable();

  /** Initializes and configures the Region and the memory to be protected
  */
  MPU_InitStruct.Enable = MPU_REGION_ENABLE;
  MPU_InitStruct.Number = MPU_REGION_NUMBER0;
  MPU_InitStruct.BaseAddress = 0x0;
  MPU_InitStruct.Size = MPU_REGION_SIZE_4GB;
  MPU_InitStruct.SubRegionDisable = 0x87;
  MPU_InitStruct.TypeExtField = MPU_TEX_LEVEL0;
  MPU_InitStruct.AccessPermission = MPU_REGION_NO_ACCESS;
  MPU_InitStruct.DisableExec = MPU_INSTRUCTION_ACCESS_DISABLE;
  MPU_InitStruct.IsShareable = MPU_ACCESS_SHAREABLE;
  MPU_InitStruct.IsCacheable = MPU_ACCESS_NOT_CACHEABLE;
  MPU_InitStruct.IsBufferable = MPU_ACCESS_NOT_BUFFERABLE;

  HAL_MPU_ConfigRegion(&MPU_InitStruct);
  /* Enables the MPU */
  HAL_MPU_Enable(MPU_PRIVILEGED_DEFAULT);

}

/**
  * @brief  Period elapsed callback in non blocking mode
  * @note   This function is called  when TIM2 interrupt took place, inside
  * HAL_TIM_IRQHandler(). It makes a direct call to HAL_IncTick() to increment
  * a global variable "uwTick" used as application time base.
  * @param  htim : TIM handle
  * @retval None
  */
void HAL_TIM_PeriodElapsedCallback(TIM_HandleTypeDef *htim)
{
  if (htim->Instance == TIM2)
  {
    HAL_IncTick();
  }
}

/**
  * @brief  This function is executed in case of error occurrence.
  * @retval None
  */
void Error_Handler(void)
{
  /* USER CODE BEGIN Error_Handler_Debug */
  /* User can add his own implementation to report the HAL error return state */
  __disable_irq();
  while (1)
  {
  }
  /* USER CODE END Error_Handler_Debug */
}
#ifdef USE_FULL_ASSERT
/**
  * @brief  Reports the name of the source file and the source line number
  *         where the assert_param error has occurred.
  * @param  file: pointer to the source file name
  * @param  line: assert_param error line source number
  * @retval None
  */
void assert_failed(uint8_t *file, uint32_t line)
{
  /* USER CODE BEGIN 6 */
  /* User can add his own implementation to report the file name and line number,
     ex: printf("Wrong parameters value: file %s on line %d\r\n", file, line) */
  /* USER CODE END 6 */
}
#endif /* USE_FULL_ASSERT */

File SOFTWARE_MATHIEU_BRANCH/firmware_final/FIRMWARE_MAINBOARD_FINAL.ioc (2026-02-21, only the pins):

Mcu.UserName=STM32H743VIHx
PA11.Signal=USB_OTG_FS_DM
PA12.Signal=USB_OTG_FS_DP
PA8.Signal=I2C3_SCL
PA9.Signal=S_TIM1_CH2
PB1.Signal=S_TIM3_CH4
PB14.Signal=USART1_TX
PB15.Signal=USART1_RX
PB7.GPIO_Label=LIDAR_SPEED
PB7.Signal=GPIO_Output
PB8.Signal=I2C1_SCL
PB9.Signal=I2C1_SDA
PC0.GPIO_Label=INT1
PC0.Signal=GPXTI0
PC1.GPIO_Label=ACCEL_CS
PC1.Signal=GPIO_Output
PC2_C.GPIO_Label=INT2
PC2_C.Signal=GPXTI2
PC9.Signal=I2C3_SDA
PD10.GPIO_Label=LED1
PD10.Signal=GPIO_Output
PD11.GPIO_Label=LED0
PD11.Signal=GPIO_Output
PD12.Signal=I2C4_SCL
PD13.Signal=I2C4_SDA
PD8.Signal=USART3_TX
PD9.Signal=USART3_RX
PE0.Signal=UART8_RX
PE1.Signal=UART8_TX
PE2.Signal=SPI4_SCK
PE5.Signal=SPI4_MISO
PE6.Signal=SPI4_MOSI
PE7.Signal=UART7_RX
PE8.Signal=UART7_TX

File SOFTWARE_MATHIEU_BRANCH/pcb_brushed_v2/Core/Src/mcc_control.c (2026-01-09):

/*
 * mcc_control.c
 *
 *  Created on: Nov 22, 2025
 *      Author: mathi
 */


//adc2in5 ntc

#include "mcc_control.h"
#include <math.h>

static PID_Params_t g_speedPidParams = {0};
static PID_Params_t g_posPidParams   = {0};

#define MOTOR_COUNT_MAX  2
extern Motor_t g_motors[2];
// ---------- Helpers internes ----------

static float clampf(float x, float minVal, float maxVal)
{
    if (x < minVal) return minVal;
    if (x > maxVal) return maxVal;
    return x;
}


void Motor_ApplyCommand(Motor_t *m)
{
    if (m->htimPwm == NULL) return;

    float u = clampf(m->cmd, -1.0f, 1.0f);
    if(fabs(u)<=0.1){
    	u=0.0;
    }

    uint32_t arr = m->htimPwm->Instance->ARR;
    float duty =1.0-fabsf(u);
    uint32_t ccrDuty = (uint32_t)(duty * (float)arr);

    if (u > 0.0f)
    {
        __HAL_TIM_SET_COMPARE(m->htimPwm, m->pwmChA, ccrDuty);
        __HAL_TIM_SET_COMPARE(m->htimPwm, m->pwmChB, arr);

    }
    else if (u < 0.0f)
    {
        __HAL_TIM_SET_COMPARE(m->htimPwm, m->pwmChA, arr);
        __HAL_TIM_SET_COMPARE(m->htimPwm, m->pwmChB, ccrDuty);
    }
    else
    {
        __HAL_TIM_SET_COMPARE(m->htimPwm, m->pwmChA, 0);
        __HAL_TIM_SET_COMPARE(m->htimPwm, m->pwmChB, 0);
    }
}

static float PID_Update(const PID_Params_t *p, PID_State_t *s,float setpoint, float measurement, float dt)
{
    float error = setpoint - measurement;

    float P = p->Kp * error;

    s->integrator += error * dt;

    if (p->Ki > 0.0f) {
        float iMax = p->outMax / p->Ki;
        if (s->integrator >  iMax) s->integrator =  iMax;
        if (s->integrator < -iMax) s->integrator = -iMax;
    }
    float I = p->Ki * s->integrator;

    float derivative = (error - s->prevError) / dt;
    float D = p->Kd * derivative;

    float out = P + I + D;

    out = clampf(out, -p->outMax, p->outMax);

    float u_dead = 0.25f;

    if((out< u_dead) && (out > -u_dead)){

    	out=0.0f;
    }
    s->prevError = error;

    return out;
}

// Mise à jour mesures à partir encodeur
//void Motor_UpdateMeasurement(Motor_t *m, float dt)
//{
//    if (m->htimEnc == NULL || dt <= 0.0f) return;
//
//    uint32_t cnt = __HAL_TIM_GET_COUNTER(m->htimEnc);
//    int32_t delta = (int16_t)(cnt - (uint16_t)m->encPrev);
//
//    m->encPrev   = cnt;
//    m->encRaw    = cnt;
//    float revs = (float)delta / m->ticksPerRev;
//
//    m->speedRps = revs / dt;
//    m->speedRpm = m->speedRps * 60.0f;
//
//    float angle_bis = m->angleDeg + revs * 360.0f;
//
//    angle_bis = fmodf(angle_bis, 360.0f);
//    if (angle_bis < 0.0f) angle_bis += 360.0f;
//
//    m->angleDeg = angle_bis;
//}

void Motor_UpdateMeasurement(Motor_t *m, float dt)
{
    int32_t pos_now = (int32_t)__HAL_TIM_GET_COUNTER(m->htimEnc);
    m->pos_buffer[m->idx] = pos_now;
    uint8_t idx_old = (m->idx + 1) % SPEED_WINDOW_MS;
    m->idx = (m->idx + 1) % SPEED_WINDOW_MS;
    if (m->filled < SPEED_WINDOW_MS) {
        m->filled++;
        m->speedRps = 0.0f;
        m->speedRpm = 0.0f;
        return;
    }
    int32_t pos_old = m->pos_buffer[idx_old];

    int16_t delta16 = (int16_t)((int16_t)pos_now - (int16_t)pos_old);
    int32_t delta_counts = (int32_t)delta16;
    float Te = dt * (float)SPEED_WINDOW_MS;

    m->speedRps = (float)delta_counts / (m->ticksPerRev * Te);
    m->speedRpm = m->speedRps * 60.0f;
}


// ---------- API impl ----------

void Motor_Init(Motor_t *m,
                TIM_HandleTypeDef *htimPwm, uint32_t chA, uint32_t chB,
                TIM_HandleTypeDef *htimEnc, uint32_t encA, uint32_t encB
                )
{
    if (m == NULL) return;

    m->htimPwm  = htimPwm;
    m->pwmChA   = chA;
    m->pwmChB   = chB;

    m->htimEnc  = htimEnc;
    m->encChA   = encA;
    m->encChB   = encB;

    m->ticksPerRev =TICK_PER_ROTOR_TURN*ENCODER_MULTIPLIER*GEAR_RATIO;

    m->encRaw  = 0;
    m->encPrev = (int32_t)__HAL_TIM_GET_COUNTER(htimEnc);
    m->speedRps = 0.0f;
    m->speedRpm = 0.0f;
    m->angleDeg = 0.0f;

    m->mode            = MOTOR_MODE_DISABLED;
    m->targetSpeedRpm  = 0.0f;
    m->targetAngleDeg  = 0.0f;
    m->angle_flag=0;
    m->cmd=0.0f;
    m->idx=0;

    m->speedPid.integrator = 0.0f;
    m->speedPid.prevError  = 0.0f;
    m->posPid.integrator   = 0.0f;
    m->posPid.prevError    = 0.0f;

}

void Motor_SetCommonSpeedPid(float Kp, float Ki, float Kd, float outMax)
{
    g_speedPidParams.Kp     = Kp;
    g_speedPidParams.Ki     = Ki;
    g_speedPidParams.Kd     = Kd;
    g_speedPidParams.outMax = outMax;
}

void Motor_SetCommonPosPid(float Kp, float Ki, float Kd, float outMax)
{
    g_posPidParams.Kp     = Kp;
    g_posPidParams.Ki     = Ki;
    g_posPidParams.Kd     = Kd;
    g_posPidParams.outMax = outMax;
}

void Motor_SetTargetSpeed(Motor_t *m, float rpm)
{
    if (m == NULL) return;
    m->mode           = MOTOR_MODE_SPEED;
    m->targetSpeedRpm = rpm;
}

void Motor_GotoAngle(Motor_t *m, float angleDeg)
{
    if (m == NULL) return;
    m->mode          = MOTOR_MODE_POSITION;
    m->targetAngleDeg = angleDeg;
}

void Motor_Disable(Motor_t *m)
{
    if (m == NULL) return;
    m->mode = MOTOR_MODE_DISABLED;
    m->cmd=0.0f;
    Motor_ApplyCommand(m);
    m->speedPid.integrator = 0.0f;
    m->posPid.integrator   = 0.0f;
}

// ---------- Tâche FreeRTOS ----------

void App_InitMotors(void)
{
	//moteur de gauche
    HAL_TIM_PWM_Start(MOT1_PWM_HTIM, MOT1_PWM_CH_A);
    HAL_TIM_PWM_Start(MOT1_PWM_HTIM, MOT1_PWM_CH_B);
    HAL_TIM_Encoder_Start(MOT1_ENC_HTIM, TIM_CHANNEL_ALL);

    //moteur de droite
    HAL_TIM_PWM_Start(MOT2_PWM_HTIM, MOT2_PWM_CH_A);
    HAL_TIM_PWM_Start(MOT2_PWM_HTIM, MOT2_PWM_CH_B);
    HAL_TIM_Encoder_Start(MOT2_ENC_HTIM, TIM_CHANNEL_ALL);

//    // Moteur 3
//    HAL_TIM_PWM_Start(MOT3_PWM_HTIM, MOT3_PWM_CH_A);
//    HAL_TIM_PWM_Start(MOT3_PWM_HTIM, MOT3_PWM_CH_B);
//    HAL_TIM_Encoder_Start(MOT3_ENC_HTIM, TIM_CHANNEL_ALL);



    Motor_Init(&g_motors[0],MOT1_PWM_HTIM, MOT1_PWM_CH_A, MOT1_PWM_CH_B,MOT1_ENC_HTIM, MOT1_ENC_CH_A, MOT1_ENC_CH_B);
    Motor_Init(&g_motors[1],MOT2_PWM_HTIM, MOT2_PWM_CH_A, MOT2_PWM_CH_B,MOT2_ENC_HTIM, MOT2_ENC_CH_A, MOT2_ENC_CH_B);
}
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

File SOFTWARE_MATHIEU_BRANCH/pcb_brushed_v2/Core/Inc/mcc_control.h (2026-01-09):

/*
 * mcc_control.h
 *
 *  Created on: Nov 22, 2025
 *      Author: mathi
 */

#ifndef INC_MCC_CONTROL_H_
#define INC_MCC_CONTROL_H_

#include "stm32g4xx_hal.h"   // adapte le nom exact
#include <stdint.h>

extern TIM_HandleTypeDef htim1;
extern TIM_HandleTypeDef htim2;
extern TIM_HandleTypeDef htim3;
extern TIM_HandleTypeDef htim4;
extern TIM_HandleTypeDef htim8;

//moteur de gauche
#define MOT1_PWM_HTIM        (&htim3)
#define MOT1_PWM_CH_A        TIM_CHANNEL_4   // PWMA
#define MOT1_PWM_CH_B        TIM_CHANNEL_3   // PWMB

#define MOT1_ENC_HTIM        (&htim2)
#define MOT1_ENC_CH_A        TIM_CHANNEL_2   // HALLA
#define MOT1_ENC_CH_B        TIM_CHANNEL_1   // HALLB



//moteur de droite
#define MOT2_PWM_HTIM        (&htim4)
#define MOT2_PWM_CH_A        TIM_CHANNEL_2   // PWMA
#define MOT2_PWM_CH_B        TIM_CHANNEL_1   // PWMB

#define MOT2_ENC_HTIM        (&htim1)
#define MOT2_ENC_CH_A        TIM_CHANNEL_2   // HALLA
#define MOT2_ENC_CH_B        TIM_CHANNEL_1   // HALLB


//#define MOT3_PWM_HTIM        (&htim3)
//#define MOT3_PWM_CH_A        TIM_CHANNEL_1   // PWMA (à confirmer)
//#define MOT3_PWM_CH_B        TIM_CHANNEL_2   // PWMB (à confirmer)
//
//#define MOT3_ENC_HTIM        (&htim8)
//#define MOT3_ENC_CH_A        TIM_CHANNEL_2   // HALLA
//#define MOT3_ENC_CH_B        TIM_CHANNEL_1   // HALLB

#define NTC_ADC              (&hadc2)
#define NTC_ADC_CHANNEL      ADC_CHANNEL_5   // correspond à ADC2_IN5


#define TICK_PER_ROTOR_TURN  12.0f
#define ENCODER_MULTIPLIER  4.0f
#define GEAR_RATIO 34.014f

#define SPEED_WINDOW_MS 20

#define RAMP_MAX  20.0f

#define ANGLE_ERROR  0.5f

#define R_WHEEL  0.02935f
#define L_DIST  0.184f


typedef enum
{
    MOTOR_MODE_DISABLED = 0,
    MOTOR_MODE_SPEED,
    MOTOR_MODE_POSITION
} MotorMode_t;

typedef struct
{
    float Kp;
    float Ki;
    float Kd;

    float outMax;
} PID_Params_t;

typedef struct
{
    float integrator;
    float prevError;
} PID_State_t;

typedef struct
{
    // --- Hardware ---
    TIM_HandleTypeDef *htimPwm;
    uint32_t pwmChA;
    uint32_t pwmChB;

    TIM_HandleTypeDef *htimEnc;
    uint32_t encChA;
    uint32_t encChB;

    float   ticksPerRev;

    // --- Mesures ---
    int32_t encRaw;
    int32_t encPrev;
    float   speedRps;
    float   speedRpm;
    float   angleDeg;
    int32_t pos_buffer[SPEED_WINDOW_MS];
    uint8_t idx;
    uint8_t filled;
    // --- Consignes ---
    MotorMode_t mode;
    float targetSpeedRpm;
    float targetAngleDeg;
    float rampdiffmax;
    float cmd;

    uint8_t angle_flag;

    // --- PID states par moteur (mais params communs) ---
    PID_State_t speedPid;
    PID_State_t posPid;

} Motor_t;


void App_InitMotors(void);
void Motor_Init(Motor_t *m,TIM_HandleTypeDef *htimPwm, uint32_t chA, uint32_t chB,TIM_HandleTypeDef *htimEnc, uint32_t encA, uint32_t encB);
void Motor_UpdateMeasurement(Motor_t *m, float dt);
void Motor_ApplyCommand(Motor_t *m);
void Motor_SetCommonSpeedPid(float Kp, float Ki, float Kd, float outMax);
void Motor_SetCommonPosPid  (float Kp, float Ki, float Kd, float outMax);
void Motor_SetTargetSpeed(Motor_t *m, float rpm);
void Motor_GotoAngle     (Motor_t *m, float angleDeg);
void Motor_Disable       (Motor_t *m);
void MotorControlTask(float dt);


#endif /* INC_MCC_CONTROL_H_ */

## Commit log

2025-09-09 DXF model of 2804 BL
    [MiToot 2804 100kv - stator.dxf]
2025-09-09 DXF + mecanique
    [MiToot 2804 100kv - stator.dxf]
2025-09-11 update foc
    [FOC_CONTROLLER_V1-B_Cu.gbr, FOC_CONTROLLER_V1-B_Mask.gbr, FOC_CONTROLLER_V1-B_Paste.gbr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]
2025-09-12 lidar test nucleo
2025-09-19 LiDAR + PAPI
    [PCB_PAPI.kicad_pcb, PCB_PAPI.kicad_sch]
2025-09-19 update pcb papi
    [1050281001.stp, 2N7002KQBZ.stp, 3670108.stp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]
2025-09-22 PCB Principal
    [accesoires.kicad_sch]
2025-09-26 up pcb principal
    [MOUSER-450001XXXXxlsx_ESE_POMMERY_ROMEO.xlsx, MOUSER-450001XXXXxlsx_ESE_POMMERY_ROMEO_PARTIE1.xlsx, MOUSER-450001XXXXxlsx_ESE_POMMERY_ROMEO_PARTIE2.xlsx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]
2025-10-03 up hall
2025-10-19 pcb v2
    [PCB_PAPI-B_Cu.gbr, PCB_PAPI-B_Mask.gbr, PCB_PAPI-B_Paste.gbr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]
2025-10-21 Update README with V2 specifications
    Added details for V2 of the motherboard and FOC STM32 based controller.
2025-10-21 Added CAD images
2025-10-30 up brushed
    [MOTOR1.kicad_sch, PCB_BRUSHED.kicad_pcb, PCB_BRUSHED.kicad_sch]
2025-11-28 lidar fonctionne bien
2025-12-04 CLusterization readable and efficient
    TODO Hole filling
2025-12-05 cluster hole handling

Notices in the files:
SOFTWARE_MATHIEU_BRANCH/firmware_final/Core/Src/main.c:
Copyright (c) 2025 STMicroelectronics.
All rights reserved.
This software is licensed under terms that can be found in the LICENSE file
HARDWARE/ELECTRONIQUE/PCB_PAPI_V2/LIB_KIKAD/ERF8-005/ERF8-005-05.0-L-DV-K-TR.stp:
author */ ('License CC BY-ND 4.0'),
